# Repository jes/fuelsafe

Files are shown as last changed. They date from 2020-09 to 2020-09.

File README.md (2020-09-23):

# FuelSafe

FuelSafe is an inline fuel sensor. It senses the presence of fuel in the line by shining an LED through a clear hose and
measuring the brightness received on a photoresistor. I made it for my [racing lawnmower](https://incoherency.co.uk/blog/tags/lawnmower.html)
so that we know if we're about to run out of fuel and can make an early pit stop instead of sputtering to a halt.

(This file is basically just notes to myself, but if you want to build one the same you might find it helpful).

## Principle

A section of clear fuel hose is contained within a 3d-printed housing. An LED shines through the hose, and a photoresistor picks up
the light from the LED. There is little to no ambient light leakage due to the housing. The photoresistor is placed as one side of
a voltage divider which allows the reading to be determined using an analogue pin on the microcontroller. The presence or
absence of fuel changes the brightness that is detected at the photoresistor. When we detect that there is no fuel present,
we switch on the output signal, which is used to power an LED to alert the driver that he is about to run out of fuel.

## Schematic

Here is a sketch of the layout for the circuit board on copper stripboard. It is somewhere between an arbitrary sketch
and a circuit schematic:

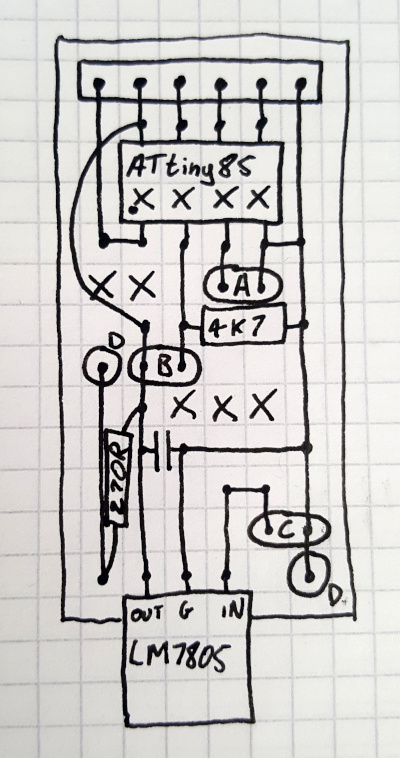
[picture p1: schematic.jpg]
Sketch of schematic


The crosses mark where the traces on the stripboard must be broken.

The 6-pin header at the top is the programming header, and the pins from left to right are:

Pin | Function
--- | ---
1 | Reset
2 | Vcc
3 | Pin 2
4 | Pin 1
5 | Pin 0
6 | GND

The other connections are labelled with letters:

Label | Function
--- | ---
A | output signal and GND
B | to photoresistor next to hose
C | input power and GND
D | to LED next to hose

There is a 270 Ohm resistor in series with the LED next to the hose. There is no resistor on the output signal (A), so one must
be supplied external to the FuelSafe if it is being used to drive an LED. There is a 4.7K Ohm resistor on the other half of the
voltage divider which is used to sense the photoresistor. There is an arbitrary filtering capacitor across the output of the
LM7805.

## Programming

Using the above table of pin assignments from the programming header, connect the ATtiny to an Arduino as per any online
instructions for programming an ATtiny with an Arduino (e.g. [these instructions](https://create.arduino.cc/projecthub/arjun/programming-attiny85-with-arduino-uno-afb829).

I used [ATTinyCore](https://github.com/SpenceKonde/ATTinyCore) with the following settings:

Board | ATtiny25/45/85 (No bootloader)
Chip | ATtiny85
Clock | 8 MHz (internal)

and the rest I think don't matter. Points to remember:

 - program the ArduinoISP sketch to the programming Arduino before starting
 - make sure there is a capacitor between reset and ground on the programming Arduino when programming the ATtiny85

## Calibration

It is not convenient to write serial output using the ATtiny85.
Therefore the code that I have written duplicates the sensor reading using `analogWrite` to pin 0. It can therefore be measured
using a multimeter or another Arduino so that you can get an idea of where the threshold should be set.

Plug the system in, run fuel through the hose and observe how the sensor reading changes, and pick a threshold value that will
discriminate between presence and absence of fuel. Note that photoresistors can drift in response to temperature so try
and pick a wide margin.

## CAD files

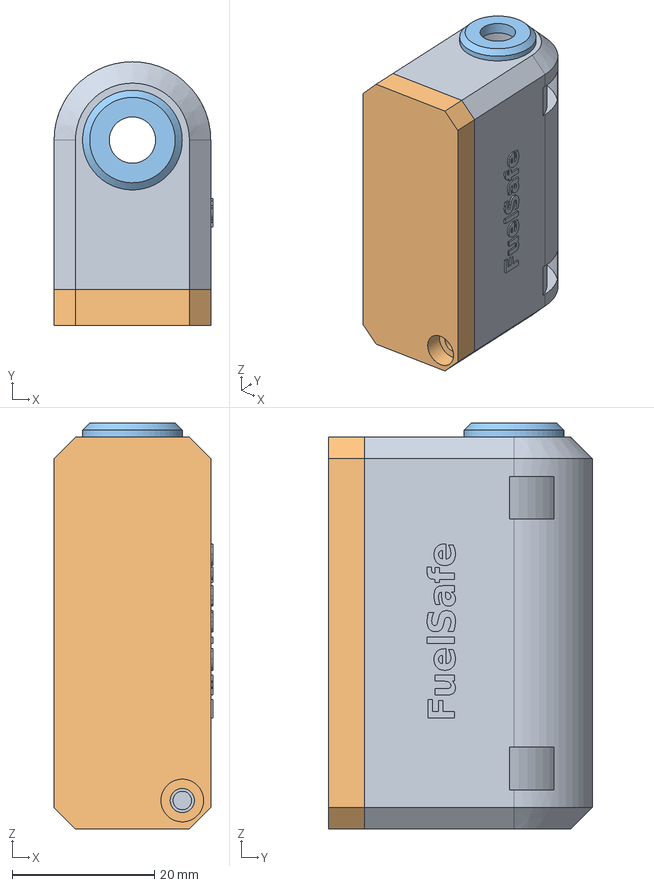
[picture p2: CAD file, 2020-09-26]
housing.fcstd
22.3 x 37.0 x 57.0 mm
Lid
Endcap

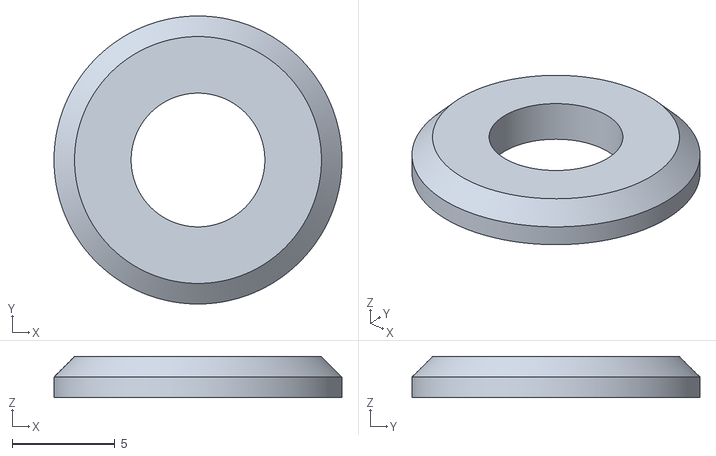
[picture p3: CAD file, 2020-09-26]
endcap.stl
14.0 x 14.0 x 2.00

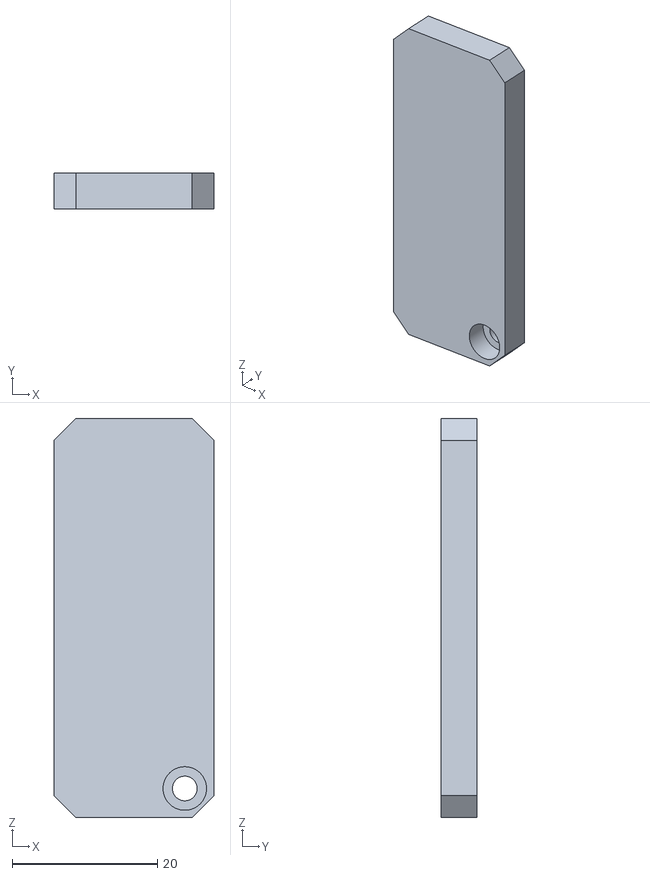
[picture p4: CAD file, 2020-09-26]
lid.stl
22.0 x 5.00 x 55.0

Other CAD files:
housing.stl

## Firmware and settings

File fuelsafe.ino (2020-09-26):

const int analogInPin = A3; // pin for photoresistor
const int analogOutPin = 0; // pin on programming header to copy photoresistor reading
const int digitalOutPin = 4; // pin for output signal

const int threshold = 430;

void setup() {
  pinMode(analogInPin, INPUT);
  pinMode(analogOutPin, OUTPUT);
  pinMode(digitalOutPin, OUTPUT);
}

void loop() {
  int sensorValue = analogRead(analogInPin);
  analogWrite(analogOutPin, sensorValue / 4);
  digitalWrite(digitalOutPin, sensorValue > threshold);
  delay(2);
}

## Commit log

2020-09-23 Shrink schematic, fix table
2020-09-23 Add first guess at Arduino sketch
2020-09-23 Fix schematic
2020-09-26 Add lid, endcap
    [endcap.stl, housing.fcstd, lid.stl]
2020-09-26 Calibrate threshold
2020-09-27 Fix schematic again
